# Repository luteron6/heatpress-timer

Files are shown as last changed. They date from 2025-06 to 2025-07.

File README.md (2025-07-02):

# heatpress-timer
The repo for my heat press timer. I created this to solve a problem with my heat press. A heat press basically has a hot metal plate that moves up and down, used to transfer vinyl, DTF transfers, and other 'transfers' to a t-shirt or other garment. The problem is that the timer must be manually stopped and started, making the process inefficient. This project seeks to automate the timer starting and stopping process by detecting when the metal plate is lowered. <br>
It all revolves around this limit switch:
<br><br><br>
When this limit switch closes, it triggers the timer:
<br><br><br>
The piezo is used to alert the user when the timer runs out of time. The plus and minus buttons allow the user to change the ammount of time the timer counts down from.
# BOM
| **Item** | **QTY Needed** | **QTY Purchased** | **Price** | **Description** | **Link** |
|---|---|---|---|---|---|
| XIAO ESP32 C6 | 1 | 1 | $9.84 | The brain! | [Link](https://www.aliexpress.us/item/3256807240718259.html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) |
| 2"" LCD Screen | 1 | 1 | $8.21 | Countdown display | [Link](https://www.aliexpress.us/item/3256808536058388.html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)|
| Vertical Limit Switches | 10 | 10 | $1.87 | Coundown reset trigger | [Link](https://www.aliexpress.us/item/3256805965729300.html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)|
| Buzzer | 1 | 10 | $2.17 | Alarm | [Link](https://www.aliexpress.us/item/3256802480381355.html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)|
| Momentary Buttons | 2 | 6 | $1.98 | Buttons to change the countdown time | [Link](https://www.aliexpress.us/item/3256804444014370.html)|
| Solder | 1 | 1 | $10.99 | Ran out of solder | [Link](https://pyrodrone.com/products/tbs-solder-spool-100g)|
| Threaded Inserts | 4 | 400 | $15.98 | Hardware for case | [Link](https://www.amazon.com/Ktehloy-Threaded-Assortment-Printing-Components/dp/B0CLKDPN65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)|
| PCB | 1 | 5 | $13.55 | Price for PCB and shipping at JLCPCB | |
| | | | | | |
| Sales Tax | | | $3.96 | | |
| Shipping | | | $11.12 | Aliexpress Shipping | |
| Shipping | | | $9.77 | Pyrodrone Shipping | |
| | | | | | |
| TOTAL | | | $89.44 | | |

There's three main parts:
### The CAD
The case! Three parts, the top/bottom of the case, and the vertical switch mount. The /CAD folder has all the parts as a STL, and everything in the STEP file. Meant to be 3D printed.

### The PCB
It connects all the electronics! It's meant to be bolted to the back of the screen. Both the KiCAD source files and the gerber files are in there.

### The Code
I designed the code to run on [CircuitPython](https://circuitpython.org/board/seeed_xiao_esp32c6/). Still a work in progress, but essentially it changes the time with the buttons (+ and -), it resets the timer when the limit switch is triggered, and beeps when the timer is at 0. The last known time is stored in the file settings.txt so that it persists across reboots. Drop/upload all the files in /Code into the REPL once CircuitPython is installed on the ESP.

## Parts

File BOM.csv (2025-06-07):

Item | QTY Needed | QTY Purchased | Price | Description | Link
XIAO ESP32 C6 | 1 | 1 | $9.84 | The brain! | https://www.aliexpress.us/item/3256807240718259.html?mp=1
2" LCD Screen | 1 | 1 | $8.21 | Countdown display | https://www.aliexpress.us/item/3256808536058388.html?mp=1
Vertical Limit Switches | 10 | 10 | $1.87 | Coundown reset trigger | https://www.aliexpress.us/item/3256805965729300.html?mp=1
Buzzer | 1 | 10 | $2.17 | Alarm | https://www.aliexpress.us/item/3256802480381355.html?mp=1
Momentary Buttons | 2 | 6 | $1.98 | Buttons to change the countdown time | https://www.aliexpress.us/item/3256804444014370.html
Solder | 1 | 1 | $10.99 | Ran out of solder | https://pyrodrone.com/products/tbs-solder-spool-100g
Threaded Inserts | 4 | 400 | $15.98 | Hardware for case | https://www.amazon.com/Ktehloy-Threaded-Assortment-Printing-Components/dp/B0CLKDPN65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
PCB | 1 | 5 | $13.55 | PCB and shipping from JLCPCB
Sales Tax |  |  | $3.96
Shipping |  |  | $11.12 | Aliexpress Shipping
Shipping |  |  | $9.77 | Pyrodrone Shipping
TOTAL |  |  | $89.44

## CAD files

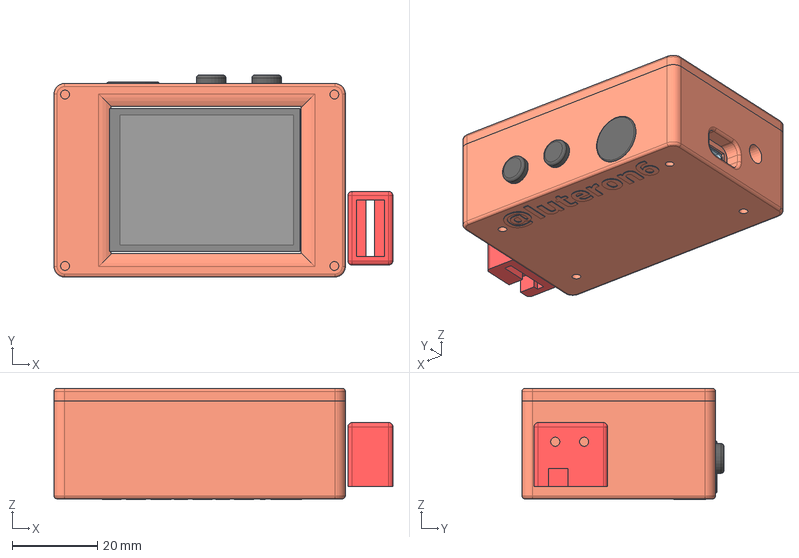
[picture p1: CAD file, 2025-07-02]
CAD/all-parts.step
79.7 x 47.5 x 26.2 mm
Base
HP2_0-8PIN-SMT
HEX_STUDS-M2XH6 x 4
PM2X5-SCREW x 4
2INCH-240X320-LCD
2INCH-LCD-MODULE-PCBA
Top
HeatPressTimer_pad_14
HeatPressTimer_pad_37
HeatPressTimer_pad_47
HeatPressTimer_pad_3
HeatPressTimer_pad_50
HeatPressTimer_pad_13
HeatPressTimer_pad_38
HeatPressTimer_pad_10
HeatPressTimer_pad_68
HeatPressTimer_pad_63
HeatPressTimer_pad_15
HeatPressTimer_pad_48
HeatPressTimer_pad_44
HeatPressTimer_pad_61
HeatPressTimer_pad_27
HeatPressTimer_pad_55
HeatPressTimer_pad_1
HeatPressTimer_pad_33
HeatPressTimer_pad_46
HeatPressTimer_pad_25
HeatPressTimer_pad_5
HeatPressTimer_pad_56
HeatPressTimer_pad_30
HeatPressTimer_pad_7
HeatPressTimer_pad_35
HeatPressTimer_pad_26
HeatPressTimer_pad_42
HeatPressTimer_pad_2
HeatPressTimer_pad_40
HeatPressTimer_PCB
HeatPressTimer_pad_65
HeatPressTimer_pad_34
HeatPressTimer_pad_32
HeatPressTimer_pad_67
HeatPressTimer_pad_29
HeatPressTimer_pad_31
HeatPressTimer_pad_49
HeatPressTimer_pad_66
HeatPressTimer_pad_53
HeatPressTimer_pad_23
HeatPressTimer_pad_8
HeatPressTimer_pad_70
HeatPressTimer_pad_62
HeatPressTimer_pad_52
HeatPressTimer_pad_59
HeatPressTimer_pad_16
HeatPressTimer_pad_6
HeatPressTimer_pad_18
HeatPressTimer_pad_54
HeatPressTimer_pad_45
HeatPressTimer_pad_43
HeatPressTimer_pad_58
HeatPressTimer_pad_41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

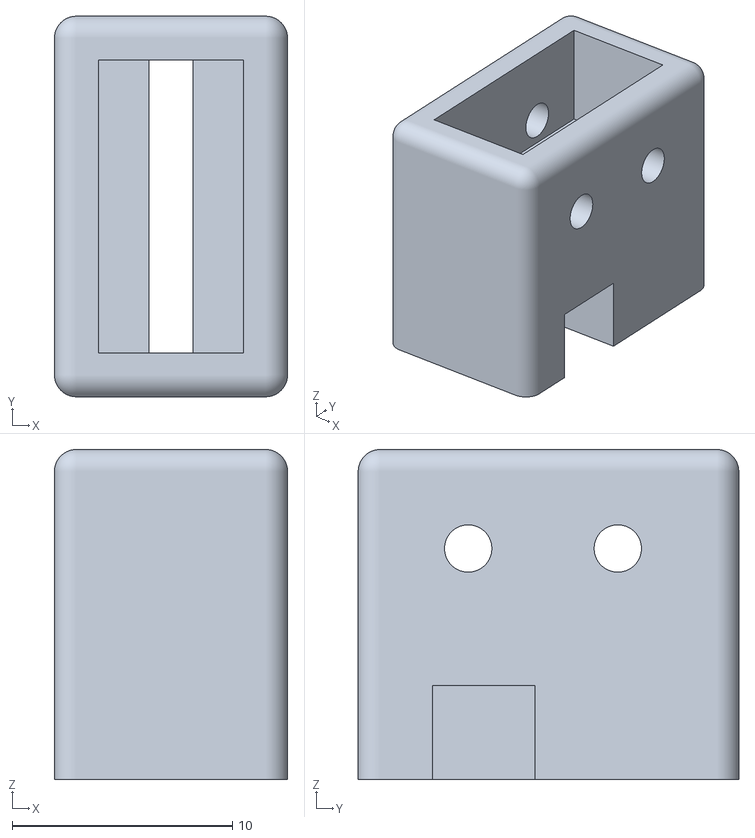
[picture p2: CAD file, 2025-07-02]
CAD/endstop-mount.stl
10.6 x 17.3 x 15.0

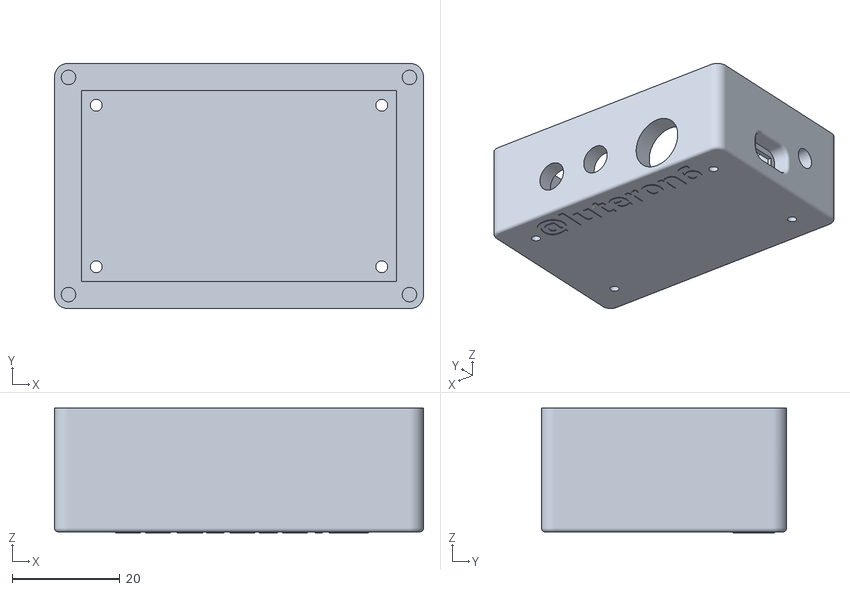
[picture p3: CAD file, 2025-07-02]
CAD/case bottom.stl
68.5 x 45.5 x 23.2

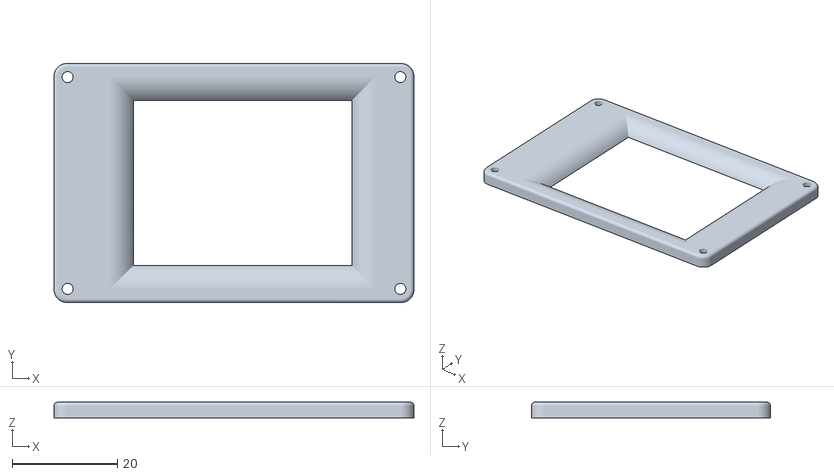
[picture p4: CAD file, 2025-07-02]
CAD/case top.stl
68.5 x 45.5 x 3.00

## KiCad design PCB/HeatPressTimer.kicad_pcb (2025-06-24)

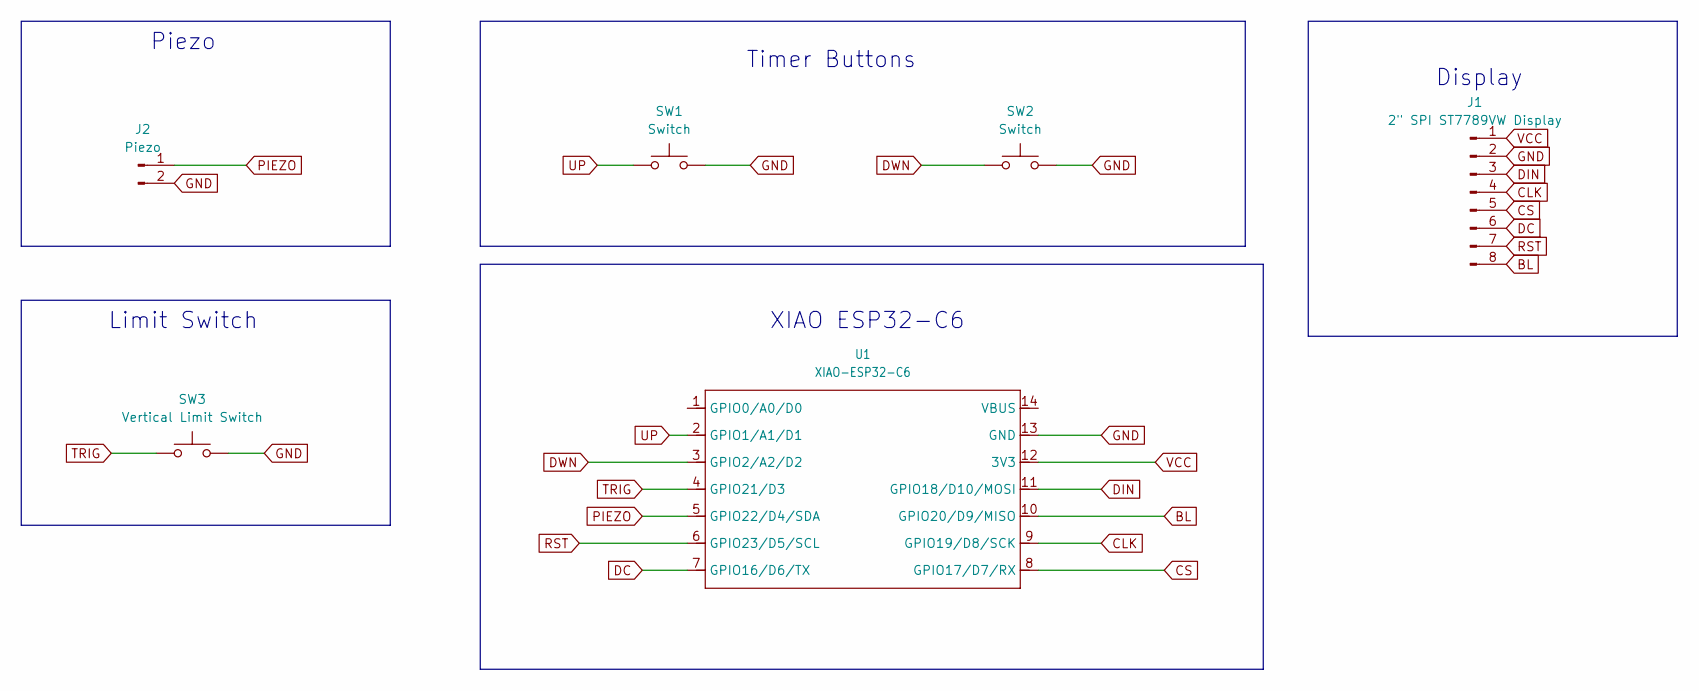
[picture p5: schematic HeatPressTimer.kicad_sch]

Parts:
J1: 2" SPI ST7789VW Display; 8-pin pads
J2: Piezo; Buzzer
SW1, SW2: Switch; 2-pin pads
SW3: Vertical Limit Switch; Vertical Switch
U1: XIAO-ESP32-C6; XIAO-ESP32C6-DIP

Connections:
BL: J1.8, U1.10 (GPIO20/D9/MISO)
CLK: J1.4, U1.9 (GPIO19/D8/SCK)
CS: J1.5, U1.8 (GPIO17/D7/RX)
DC: J1.6, U1.7 (GPIO16/D6/TX)
DIN: J1.3, U1.11 (GPIO18/D10/MOSI)
DWN: SW2.1, U1.3 (GPIO2/A2/D2)
GND: J1.2, J2.2, SW1.2, SW2.2, SW3.2, U1.13 (GND)
PIEZO: J2.1, U1.5 (GPIO22/D4/SDA)
RST: J1.7, U1.6 (GPIO23/D5/SCL)
TRIG: SW3.1, U1.4 (GPIO21/D3)
UP: SW1.1, U1.2 (GPIO1/A1/D1)
VCC: J1.1, U1.12 (3V3)

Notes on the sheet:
XIAO ESP32-C6
Piezo
Limit Switch
Timer Buttons
Display

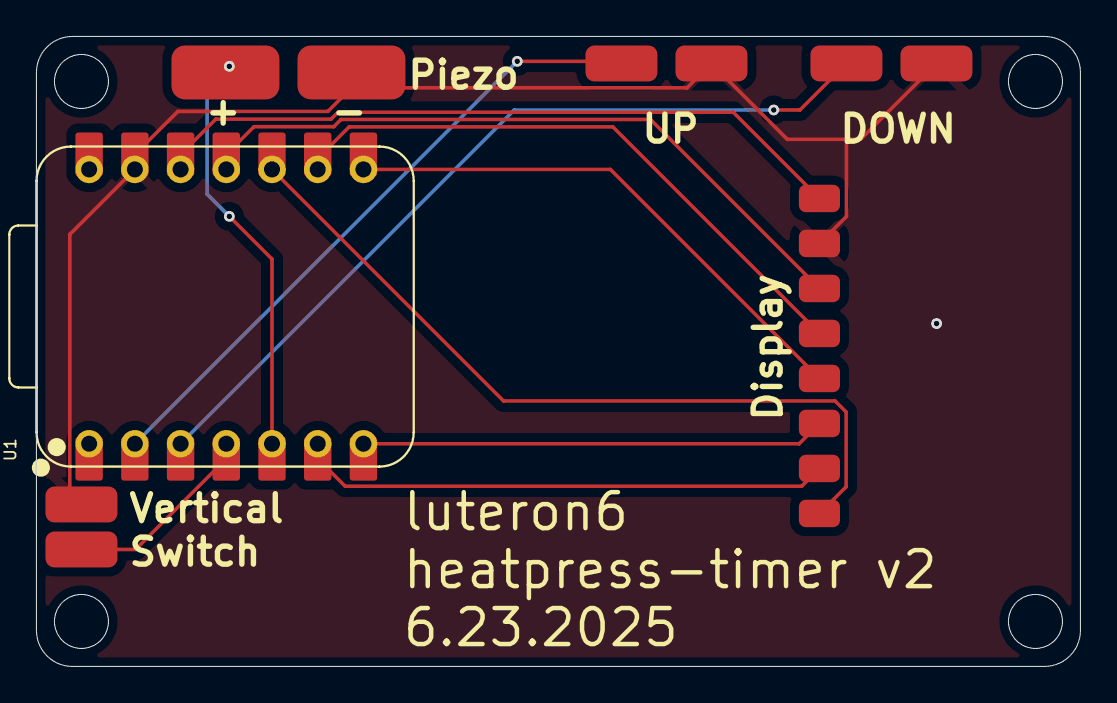
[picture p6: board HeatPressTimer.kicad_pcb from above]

Board: 2 copper layers, 58.0 x 35.0 mm, 6 parts (0 on the bottom side), 12 nets.

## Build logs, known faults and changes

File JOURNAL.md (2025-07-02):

---
title: "Heat Press Timer"
author: "@luteron6"
description: "An automatic timer for a heat press. No more phone stopwatches!"
created_at: "2025-05-19"
---

# Heat Press Timer
Made by: @luteron6

Total hours so far: 24

Estimated Cost: $89.44 (including tax, shipping, and fees)

I have a heat press that I use to transfer DTF transfers. It's basically two pieces of metal that clamp down together. The top half heats up really hot to activate the transfer's adhesive backing. The only problem is that the DTF transfer needs a specific time in the heat press, and we haven't had a good solution to tracking that time. This project is an attempt to solve that problem.

## Day 1 - 5/19/2025 - 9:22 PM (2 hours)
Before I get started, I want to outline my goals:
* The timer will be automatically started by the close of the heat press.
* A display to counting down until the heat press should be lifted.
* A buzzer to alert me when it's done.
* Two buttons to change the length of the timer.

Today I drew up a schematic for my project. I've used a SeeedStudio XIAO RP2040 before, so I'm going to try to use that again. No idea if it will have enough pins.
I also researched some parts, mostly on Amazon. Here's what I've found:
* [RP 2040](https://www.amazon.com/Microcontroller-Dual-Core-MicroPython-CircuitPython-Interfaces/dp/B09NNVNW7M/): $9.99
* [2" LCD Screen](https://www.amazon.com/2inch-IPS-LCD-Display-Module/dp/B082GFTZQD/): $14.39
* [Vertical Limit Switch](https://www.amazon.com/HUAREW-Vertical-Mechanical-3018-PROVer-3018-MX3/dp/B0B38X86NY/): $11.99
* [Buzzer](https://www.amazon.com/Gikfun-Terminals-Passive-Electronic-Arduino/dp/B01GJLE5BS/): $7.28
* [Momentary Buttons](https://www.amazon.com/Gebildet-250VAC-Prewired-Momentary-Railway/dp/B083JWJPW5/): $7.99
* Total Estimated Costs: $51.64

I also created this repo for my journal any other files. Furthermore, I tried to draw up a rough schematic for the timer:



## Day 2 - 5/20/2025 - 11:28 AM (3 hours)
Today I made a [PR](https://github.com/hackclub/highway/pull/58) to add my project to the submissions.yml file in the hackclub/highway repo.

I also tried to figure out how to connect the SPI display to the RP2040. This is my first time using the SPI protocol, and there's a lot more wires than the I2C protocol. Here's what I came up with:<br>
<br>
I also started to layout the schematic in KiCad. I haven't used KiCad in a while, so I had to figure everything out with the footprints and stuff. Here's what I have so far:<br>
<br>

## Day 2 (Session 2) - 5/20/2025 - 3:09 PM (30 minutes)
OK! I just saw the 'Sourcing parts' page on the Highway docs. I literally found all the same parts on Aliexpress for a lot cheaper. Hopefully it's not a scam. I also needed some solder. Here are the new parts:
* [XIAO RP2040](https://www.aliexpress.us/item/3256807240972277.html): $7.49
* [2" SPI LCD Display](https://www.aliexpress.us/item/3256808536058388.html): $8.21
* [Momentary Push Buttons (black)](https://www.aliexpress.us/item/3256804444014370.html): $2.00
* [Limit Switches (with handle)](https://www.aliexpress.us/item/3256805965729300.html): $1.34
* [Buzzer](https://www.aliexpress.us/item/3256802480381355.html): $2.17
* [Solder](https://pyrodrone.com/products/tbs-solder-spool-100g): $10.99
* New Total: $32.20<br>

## Day 3 - 5/21/2025 - 3:02 PM (3.5 hours)
Today I drew up what I think I want the case to look like:<br>
thumbnail_IMG_1362

I also edited my schematic:<br>


The vertical switch will be outside the case, connected by a wire. The buttons (to change the length of the timer) are on the top, and so is the piezo buzzer.
I also designed a PCB to be mounted to the back of the screen (still needs a lot of work):<br>




## Day 4 - 5/22/2025 - 5:26 PM (2 hours)
Today I refined my PCB. I think it's almost done:<br>
<br>
I added holes, filleted the corners, and made the buzzer pads wider. I intend to solder the buzzer directly to the PCB, and I don't know how wide the terminals are. I also routed the PCB. I don't know what size the standoffs/screws are on the display, so I'll have to see when I get it. Next I'll have to work on the case, then the code.

## Day 5 - 5/23/2025 - 9:32 PM (4 hours)
I decided to add my name, date, and title to the PCB. The I exported it as a STEP file for doing CAD later. I also found the STEP file for the display, so I could put them together in Onshape. Then I worked in Onshape for the rest of my time, making the case. The longest part was probably figuring out what I wanted to make the tolerances, and also the heat press inserts and screws. I'm also really new to CAD and Onshape, most of the time I was looking up tutorials and how-to guides. Anyway, I decided I will try and use M2 hardware (hopefully it's M2), but I'll buy the screen first to see what size the standoffs are. Below is my screen and PCB:<br>
<br>
Here's the hardware in my case:<br>
<br>

## Day 6 - 5/25/2025 - 8:20 PM (2 hours)
Phew! Yesterday was crazy and I couldn't find time to work on this. But I thought about it last night, and itoccurred to me that the RP2040 doesn't have wifi. So it won't have the interactive CircuitPython web interface. So I switched to the [XIAO ESP32 C6](https://www.seeedstudio.com/Seeed-Studio-XIAO-ESP32C6-p-5884.html). Here's the actual [Aliexpress link](https://www.aliexpress.us/item/3256807240718259.html) ($9.84). I also rerouted my PCB.<br>
I also forgot to add a hole for the USB-C port on the XIAO. I also filleted the edges of the case and the USB-C port. Here's what I came up with:<br>
<br>
Now for the code. It took me a while to find drivers (CircuitPython libraries) for the display. The hardest part is not being able to run the code - once I get the parts it'll be so much easier.

## Day 7 - 5/30/2025 - 10:27 PM (4 hours)
OK! I think it's done. I finished my code, created my BOM.csv, exported the gerbers, the case STEP file and STLs, and added everything to this repo. I also updated the readme.

## Day 8 - 6/7/2025 - 11:23 AM (3 hours)
I updated my README with a BOM, added my PCB to the BOM (I forgot earlier), and edited my case to add some flair. Here's pictures of my new case:
<br><br>


<br>

## Day 9 - 9:16 PM (2 hours)
Ok! We're back in business. I got some of the stuff I ordered today. Most notably, I got the ESP32-C6. I did not know it lacks native USB, so it took me a while to figure it out. I followed this [Adafruit tutorial](https://learn.adafruit.com/circuitpython-with-esp32-quick-start/web-serial-esptool). Basically, I enabled "Experimental Web Platform features" on my Chrome-based web browser, then I flashed the [.bin](https://circuitpython.org/board/seeed_xiao_esp32c6/) file to the board using Adafruit's [web serial tool](https://circuitpython.org/board/seeed_xiao_esp32c6/). Following [these](https://learn.adafruit.com/circuitpython-with-esp32-quick-start/setting-up-web-workflow) instructions, I had to install PuTTY on my laptop and connect to the ESP's serial port. Then I used these commands to initialize the wifi:
```
f = open('settings.toml', 'w')
f.write('CIRCUITPY_WIFI_SSID = "wifissid"\n')
f.write('CIRCUITPY_WIFI_PASSWORD = "wifipassword"\n')
f.write('CIRCUITPY_WEB_API_PASSWORD = "webpassword"\n')
f.close()
```
And it worked! Then I went to the IP address that was in the top of the PuTTY window, and there was the [REPL](https://learn.adafruit.com/welcome-to-circuitpython/the-repl)!

## Day 10 - ~11:30 last night (3 hours)
Yesterday was crazy, so I didn't find time to work on this project until last night. I stayed up until about 11:30, and didn't have enough energy to write this journal. So here I am today, at ~10:45 writing last night's journal.
Anyway, I soldered the XIAO to the PCB (SMD-style), and I wired up the buzzer and one of the switches. Unfortunately, the XIAO pad on my PCB wasn't connected to the pad on the buzzer (even though the pad was there), because the net tag in KiCAD was overlapping too much. I fixed all the problems and pushed all the changes to this repo (even the gerber files).

I also had to troubleshoot my code, because it used some wrong libraries and logic. I also don't have the screen yet so I can't test that. But I got the buttons and the buzzer working! My case dimensions were also off, so I had to change some of the dimensions. I reprinted the case and it should be good now.

## Day 11 - 2:09 PM (4 hours)
It's finally done!
I printed my case again, because there wasn't enough clearance in for the screen. Now it's taller and has mounts for the screen inside. It turns out the standoffs on the screen are M2, so I just added holes for M2 screws on the bottom of the case. I didn't have any M2 standoffs, so I had to use simple holes.
<br><br>

I also reworked my code, added the IP address on the top of the screen, the password, and a little note on the bottom:

https://github.com/user-attachments/assets/c68a85d8-97f3-4bc8-905b-5248fefed33b

And it pretty much works! Thank you Hack Club for funding this project!

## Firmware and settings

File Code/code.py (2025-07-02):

import board
import digitalio
import displayio
from fourwire import FourWire
from adafruit_st7789 import ST7789
import time
from adafruit_display_text import label
import pwmio
import terminalio
import wifi
from adafruit_bitmap_font import bitmap_font

# Load font
font = bitmap_font.load_font("/fonts/LeagueSpartan-Bold-16.bdf")

# Import last saved timer value from time.txt
def load_sec():
    try:
        with open("/settings.txt", "r") as f:
            return float(f.read())
    except Exception:
        return 8  # default value if file not found or invalid

def save_sec(value):
    with open("/settings.txt", "w") as f:
        f.write(str(value))

sec = load_sec()

#Setup the piezo, trigger, +, and - buttons
# Timer UP button
up = digitalio.DigitalInOut(board.A1)
up.direction = digitalio.Direction.INPUT
up.pull = digitalio.Pull.UP

# Timer DOWN button
down = digitalio.DigitalInOut(board.A2)
down.direction = digitalio.Direction.INPUT
down.pull = digitalio.Pull.UP

#Trigger
trigger = digitalio.DigitalInOut(board.D3)
trigger.direction = digitalio.Direction.INPUT
trigger.pull = digitalio.Pull.UP

#Buzzer (passive)
buzzer_pin = board.D4
buzzer = pwmio.PWMOut(buzzer_pin, duty_cycle=0, frequency=1000)  # 1kHz frequency

# Setup display
displayio.release_displays()
spi = board.SPI()
while not spi.try_lock():
    pass
spi.configure(baudrate=24000000)
spi.unlock()

display_bus = FourWire(spi, command=board.D6, chip_select=board.D7, reset=board.D5)
display = ST7789(display_bus, width=320, height=240, rotation=90,)

splash = displayio.Group()
display.root_group = splash


color_bitmap = displayio.Bitmap(320, 240, 1)
palette = displayio.Palette(3)
palette[0] = 0x000000  # Black
palette[1] = 0xFFFFFF  # White
palette[2] = 0xFF0000  # Red

num_disp = displayio.TileGrid(color_bitmap, pixel_shader=palette, x=0, y=0)
splash.append(num_disp)

timer_label = label.Label(font, text=str(sec), color=0xFFFFFF, x=135, y=120, scale=1)
splash.append(timer_label)
#end display setup

ip_address = wifi.radio.ipv4_address
#Display IP and password on screen
ip_label = label.Label(terminalio.FONT, text="IP: " + str(ip_address) + "  PW:password", color=0xFFFFFF, x=5, y=10)
splash.append(ip_label)

hc = label.Label(terminalio.FONT, text="made with love by a hack clubber", color=0xFFFFFF, x=130, y=232)
splash.append(hc)

#End IO setup
counting_down = False

while True:
    #If the up button is pressed, increase the timer by 0.5 seconds. Save sec to file. Update the display.
    if not up.value:
        sec += 0.5
        buzzer.duty_cycle = 2**15
        time.sleep(0.04)
        buzzer.duty_cycle = 0
        timer_label.text = "{:.2f}".format(sec)
        save_sec(sec)
        time.sleep(0.04)

    #If the down button is pressed, decrease the timer by 0.5 seconds. Save sec to file. Beep. Update the display.
    if not down.value:
        sec -= 0.5
        buzzer.duty_cycle = 2**15
        time.sleep(0.04)
        buzzer.duty_cycle = 0
        save_sec(sec)
        if sec < 1: #can't be less than 1 second timer
            sec = 1
        timer_label.text = "{:.2f}".format(sec)
        time.sleep(0.04)

    while trigger.value:
        # If the heat press is opened, reset the timer and display.
        timer_label.text = "{:.2f}".format(sec)
        closed = False
        time.sleep(0.05)
        break

        #If the heat press is closed, prevent the timer from starting again until it is opened.
    while not trigger.value:
        time.sleep(0.05)
        closed = True
        break
    
    #If the heat press is closed, start the timer and display the countdown.
    if not trigger.value and closed:
        start = time.monotonic()
        end = start + sec
        while time.monotonic() < end and not trigger.value:
            remaining = max(0, end - time.monotonic())
            timer_label.text = "{:04.2f}".format(remaining)
            time.sleep(0.05)
            if trigger.value:
                break
            if remaining <= 0.1:
                while True:
                    timer_label.text = "0.00"
                    palette[0] = 0xFF0000
                    buzzer.duty_cycle = 2**15
                    time.sleep(0.1)  # Buzzer on for half a second
                    palette[0] = 0x000000
                    # Turn off the buzzer
                    buzzer.duty_cycle = 0  # Turn off
                    time.sleep(0.1)  # Pause for half a second
                    if trigger.value:
                        break               
                break

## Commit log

2025-05-31 Added CAD, Code, and PCB files!
    [timer bottom.stl, timer top.stl]
2025-05-31 Added source files and BOM
    [BOM.csv, HeatPressTimer.kicad_pcb, HeatPressTimer.kicad_sch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]
2025-05-31 Added description to BOM
    [BOM.csv]
2025-06-07 Added BOM
2025-06-07 added PCB to BOM
    [BOM.csv]
2025-06-07 Updated case screenshot
2025-06-07 Updated CAD files
    [case bottom.stl, case top.stl]
2025-06-23 new PCB files
    [HeatPressTimer.kicad_pcb, HeatPressTimer.kicad_sch]
2025-06-24 Added filled zone to PCB
    [HeatPressTimer.kicad_pcb]
2025-07-02 Fixed CAD
    Made base taller, added vertical endstop mount.
    [all-parts.step, case bottom.stl, case top.stl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]
2025-07-02 Added working code
    Fixed code, added libraries and fonts
    [code.py]
